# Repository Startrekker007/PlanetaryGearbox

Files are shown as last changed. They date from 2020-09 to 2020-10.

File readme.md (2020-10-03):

The submission for the assignment is in the folder FinalAssembly. Within there is another readme.md file which consists of the summary of the project.

The _Old folder consists of the working files during the project and they don't need to be seen, they're just in the git repository in case.

Viewing on Github is easier to read and view therefore the link is https://github.com/Startrekker007/PlanetaryGearbox

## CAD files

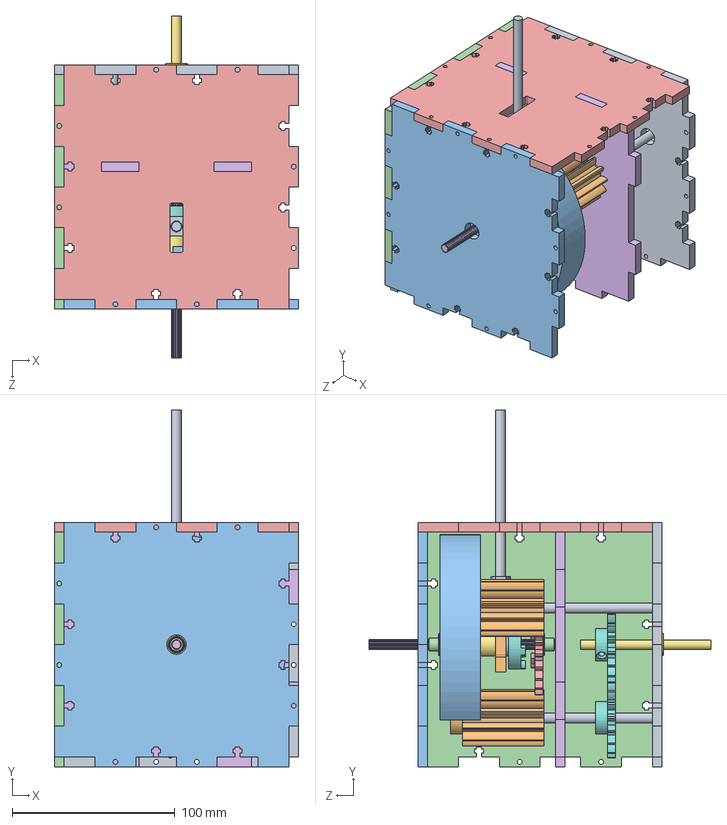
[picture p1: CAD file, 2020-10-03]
FinalAssembly/FinalAssemblyAnimation.SLDASM
150.0 x 218.9 x 210.0 mm
Shaft80mm
InputGear x 2
Shaft130mm x 4
PlanetGear x 3
RingGear
3x6ID_12OD_Flanged_Bearing x 2
SpacingWasher x 2
SunGear
SplinedShaft120mm
DogToothCollar
DogToothEnd
ShiftHolder
12mmID_Bearing

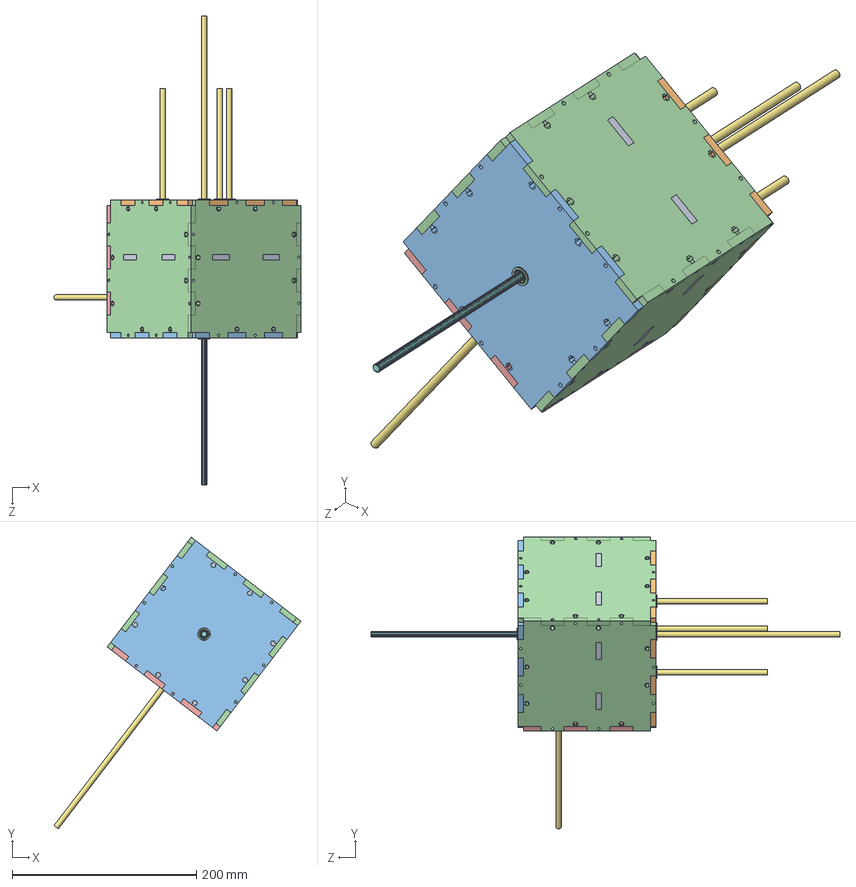
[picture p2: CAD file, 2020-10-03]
Saladworks/GearBoxWorking.SLDASM
268.0 x 316.5 x 509.0 mm
TripleInternal
InputSide
OutputSide
SlottedSide x 3
TopSide
InputGear x 2
Shaft250mm x 5
SplinedShaft250mm
planetgear x 3
sun
RingGear
535096.STEP
535096 bearing.STEP
CorrectDogTeeth
DoggedCollar
ShiftHolder

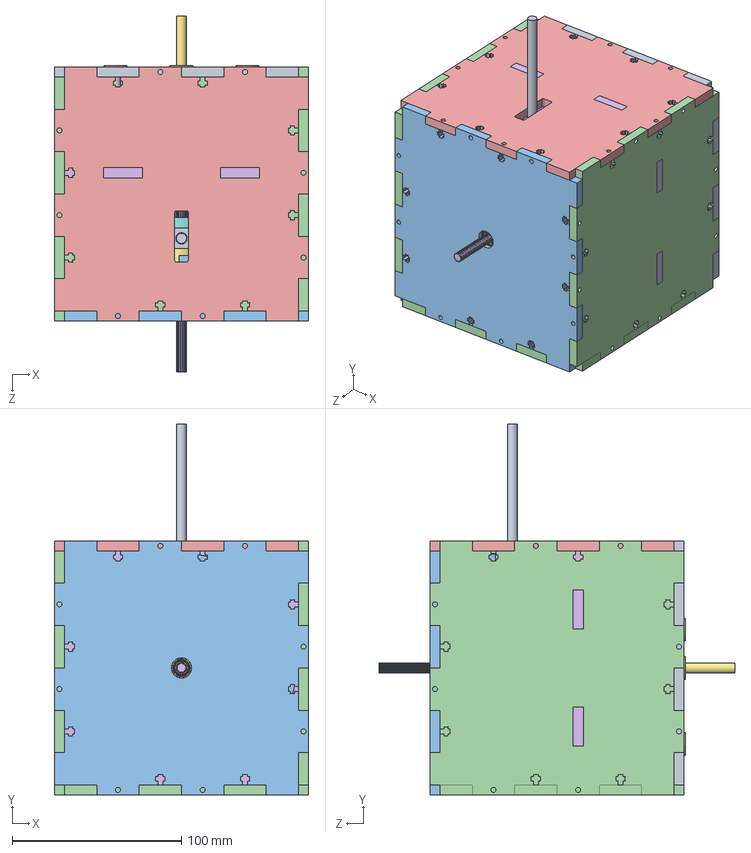
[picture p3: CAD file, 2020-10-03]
FinalAssembly/FinalAssembly.SLDASM
150.0 x 218.9 x 210.0 mm
InputSide
3x6ID_12OD_Flanged_Bearing x 11
OutputSide
SlottedSide x 3
TopSide
InternalWall
Shaft80mm
InputGear x 2
Shaft130mm x 4
PlanetGear x 3
RingGear
SpacingWasher x 2
SunGear
SplinedShaft120mm
DogToothCollar
DogToothEnd
ShiftHolder
12mmID_Bearing

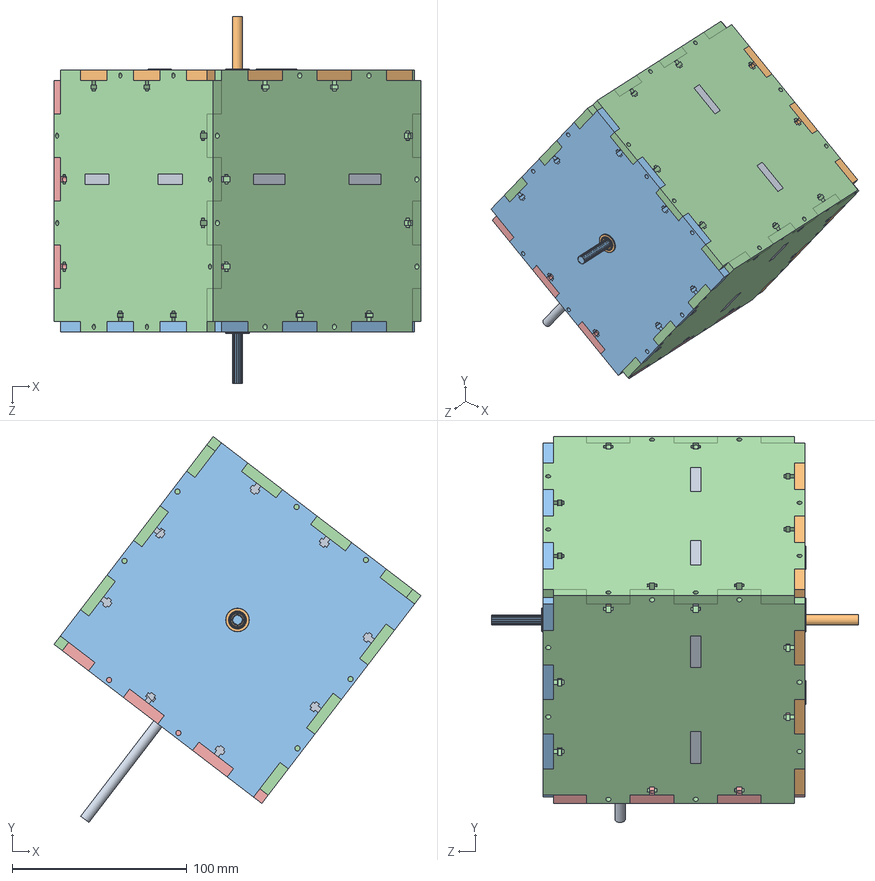
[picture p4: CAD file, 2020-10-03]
Saladworks/GearBoxRightLength.SLDASM
210.3 x 221.2 x 210.3 mm
TripleInternal
InputSide
OutputSide
SlottedSide x 3
TopSide
InputGear x 2
planetgear x 3
sun
RingGear
535096.STEP
535096 bearing.STEP
CorrectDogTeeth
DoggedCollar
ShiftHolder
Shaft130mm x 4
Shaft80mm
SplinedShaft120mm

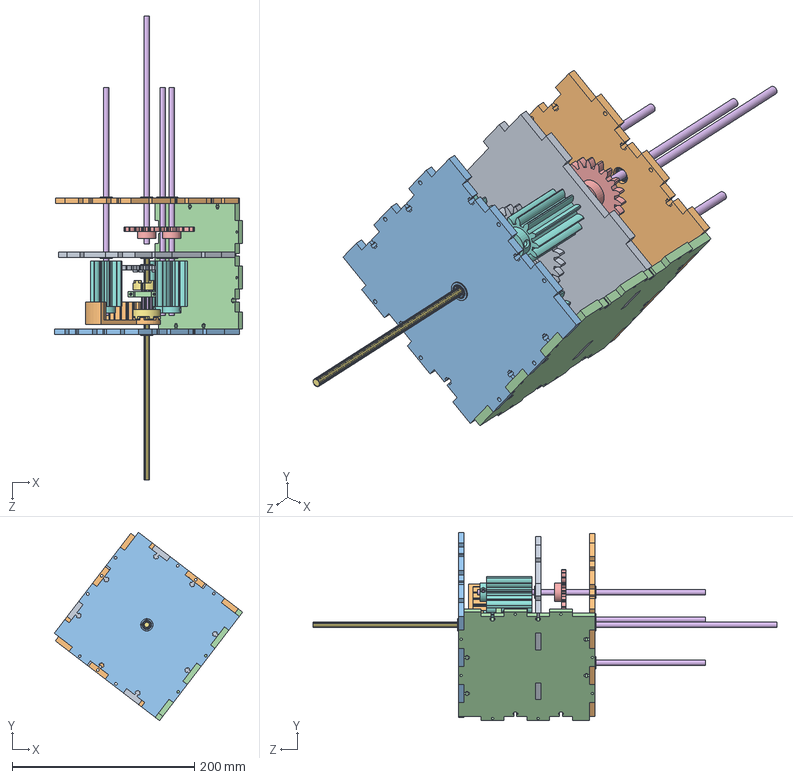
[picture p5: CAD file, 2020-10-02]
Saladworks/GearBox2019.SLDASM
206.6 x 206.6 x 509.0 mm
InputGear x 2
Shaft250mm x 4
SplinedShaft250mm
planetgear x 3
sun
RingGear
535096.STEP
535096 bearing.STEP
CorrectDogTeeth
DoggedCollar

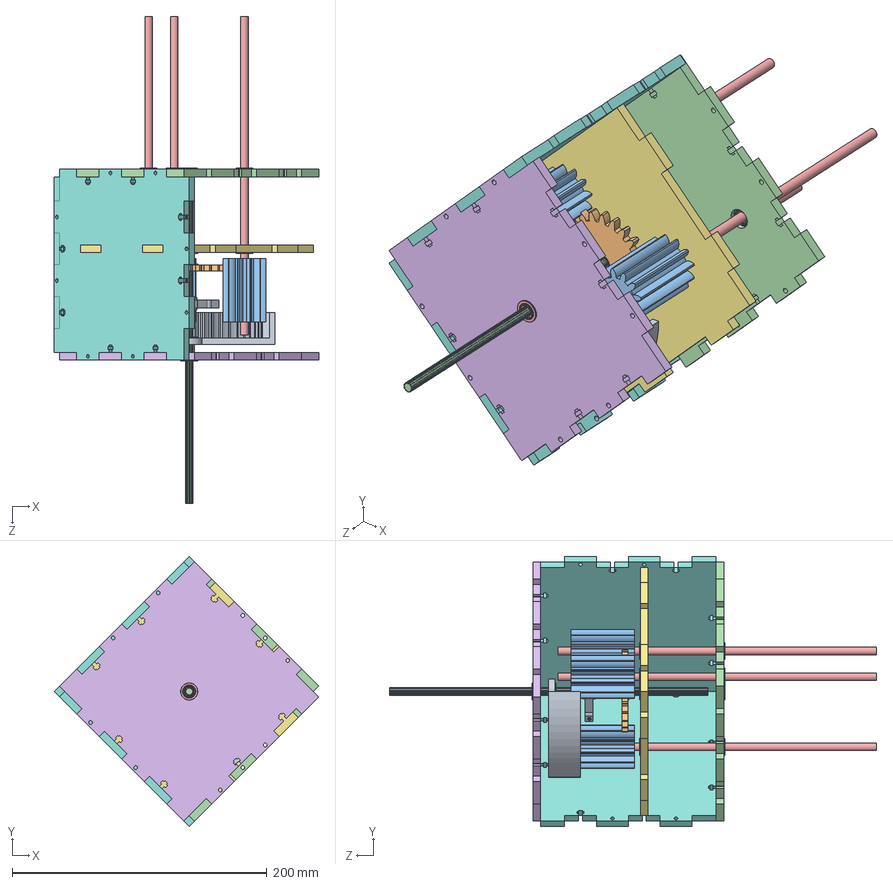
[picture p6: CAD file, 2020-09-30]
Saladworks/GearsWithBoxDemo.SLDASM
207.9 x 212.1 x 382.5 mm
RingGear
sun
planetgear x 3
SplinedShaft250mm
Shaft250mm x 3
5352201.STEP x 2
5352202.STEP x 2
5352203.STEP x 2
535096.STEP
535096 bearing.STEP
Collar
InputSide
535220.step x 9
OutputSide
TripleInternal
SlottedSide x 2

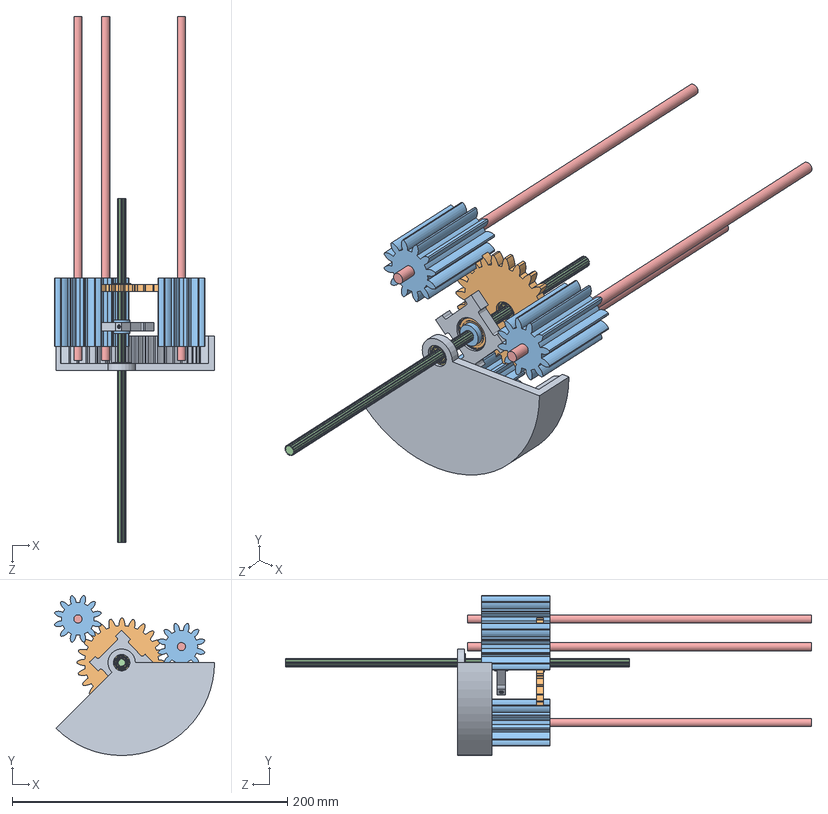
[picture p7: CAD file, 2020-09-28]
Saladworks/RealGears.SLDASM
116.3 x 116.3 x 382.5 mm
RingGear
sun
planetgear x 3
SplinedShaft250mm
Shaft250mm x 3
5352201.STEP x 2
5352202.STEP x 2
5352203.STEP x 2
535096.STEP
535096 bearing.STEP
Collar

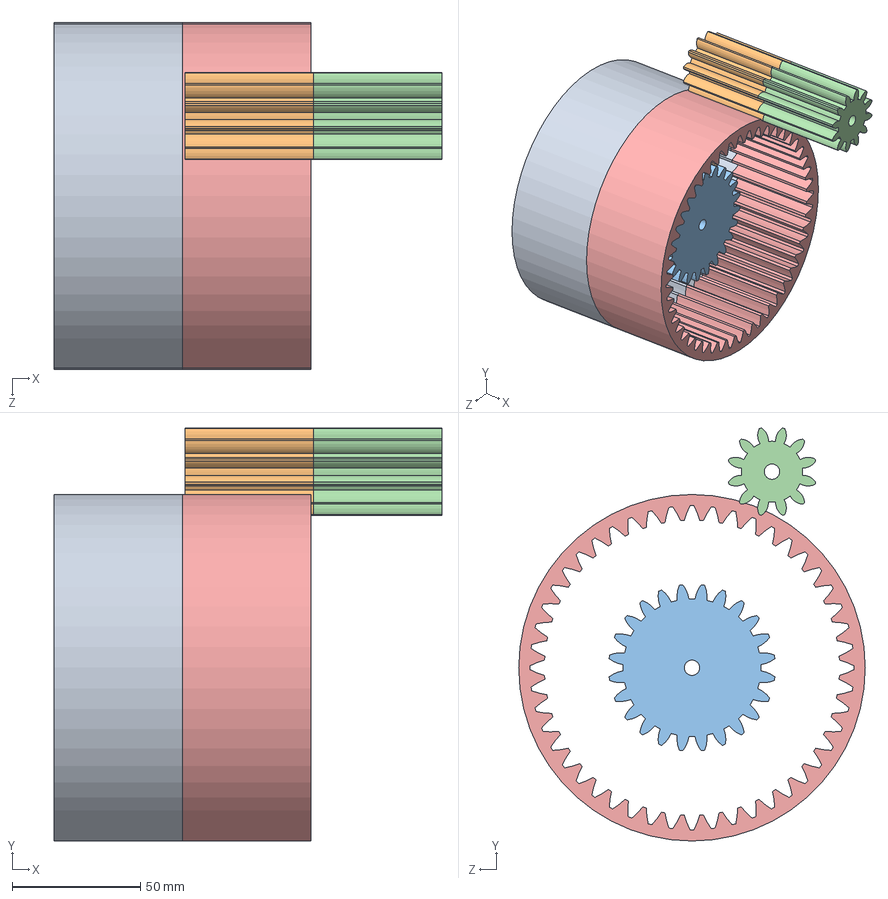
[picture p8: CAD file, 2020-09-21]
Saladworks/Planetary3.SLDASM
151.0 x 160.9 x 135.0 mm
internal spur gear_am
spur gear_am x 2
sun
PlanetGear
RingGear

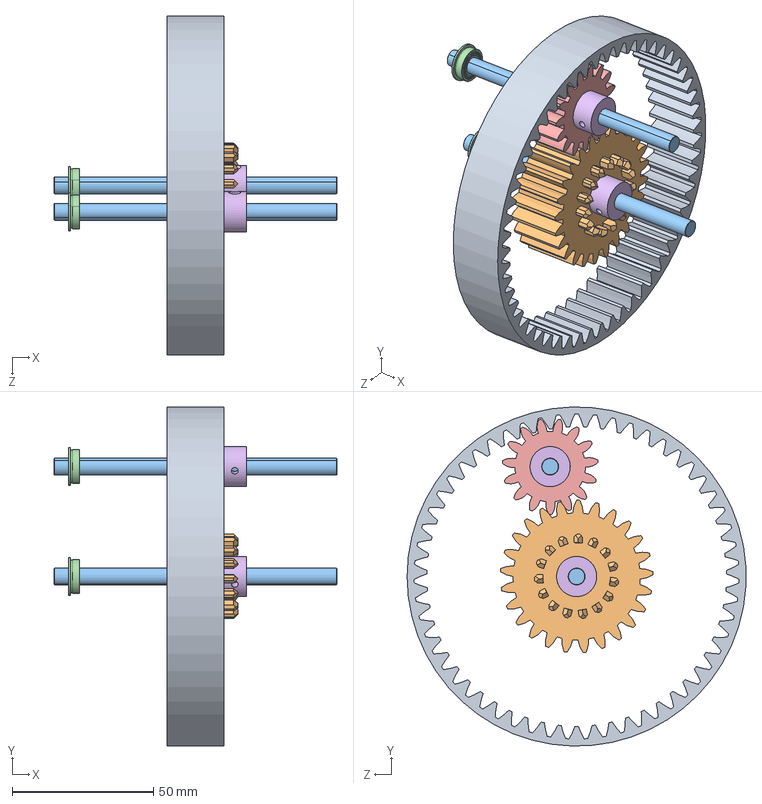
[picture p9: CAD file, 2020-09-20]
Saladworks/Gears.SLDASM
100.0 x 119.9 x 119.9 mm
internal spur gear_am
sungear
2100-0006-0100.step x 2
535220.step x 2
spur gear_am
ShaftStopper x 2

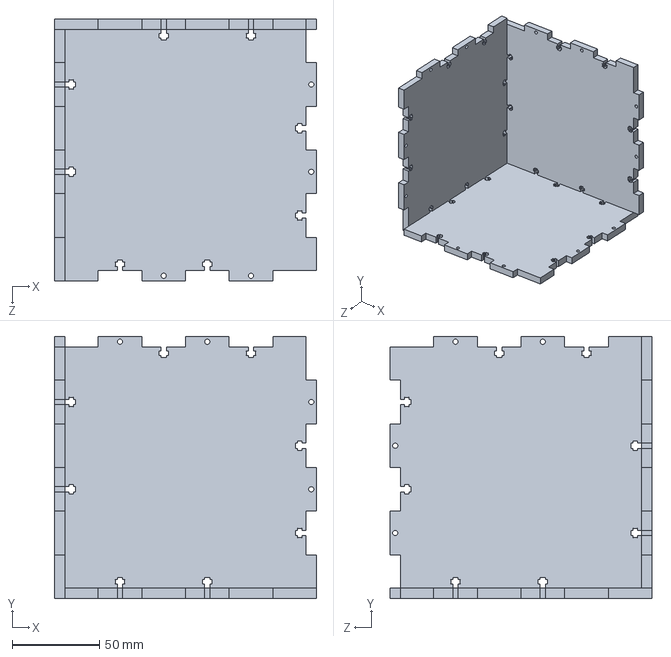
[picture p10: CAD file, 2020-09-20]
Saladworks/Assembledemo.SLDASM
150.0 x 150.0 x 150.0 mm
BlankSide x 3

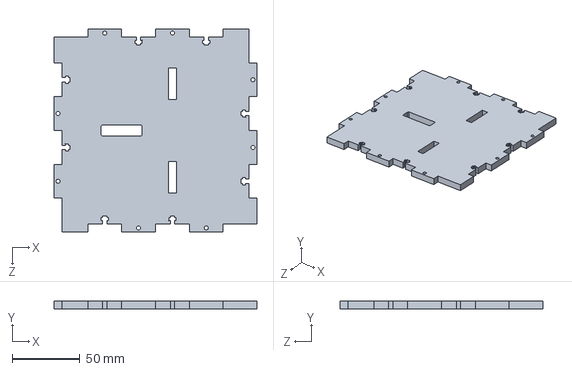
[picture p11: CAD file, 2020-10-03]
FinalAssembly/AcrylicCase/TopSide.SLDPRT
150.0 x 6.00 x 150.0 mm

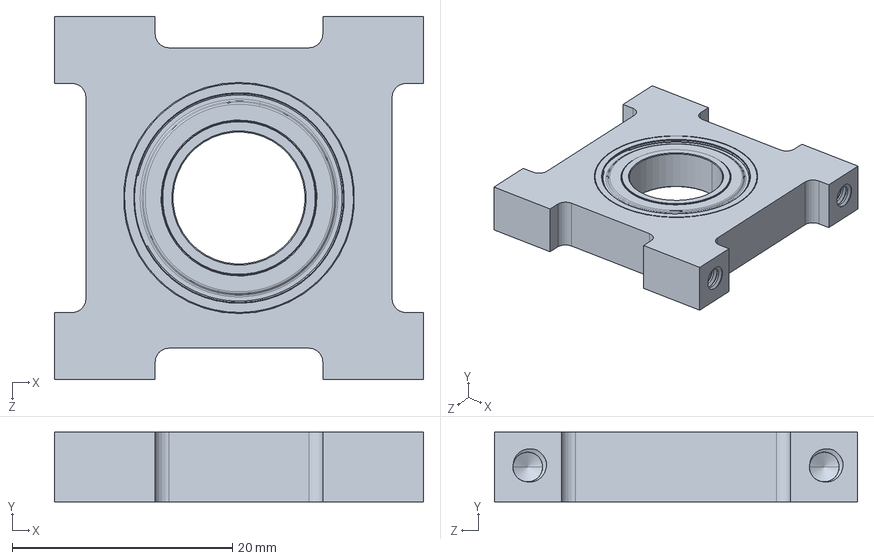
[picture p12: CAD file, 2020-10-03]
FinalAssembly/Bearings/12mmID_Bearing.SLDPRT
33.5 x 6.35 x 33.0 mm

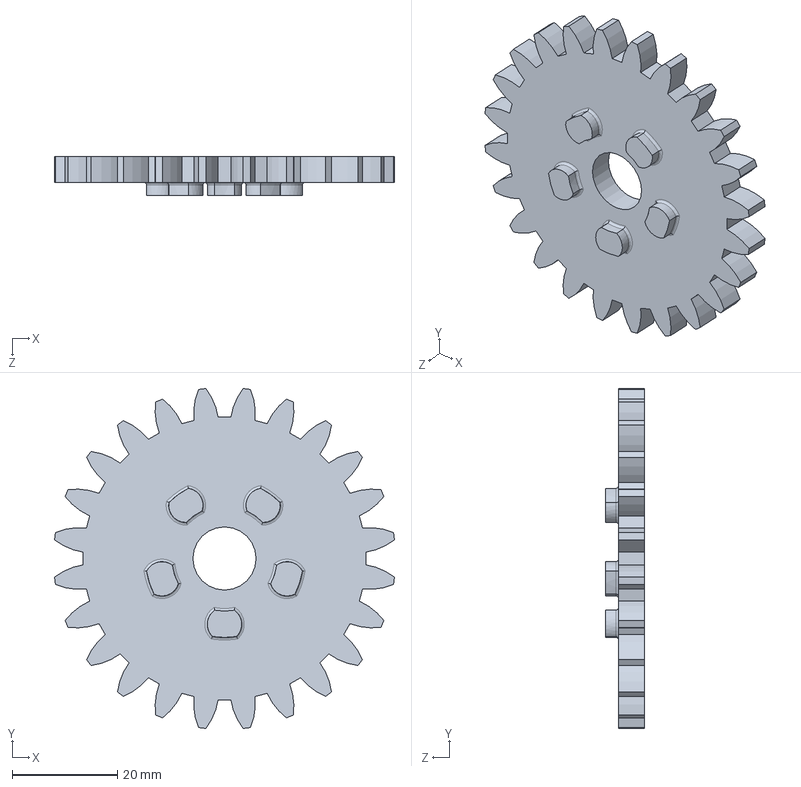
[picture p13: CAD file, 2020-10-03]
FinalAssembly/Gears/SunGear.SLDPRT
64.6 x 64.6 x 7.50 mm

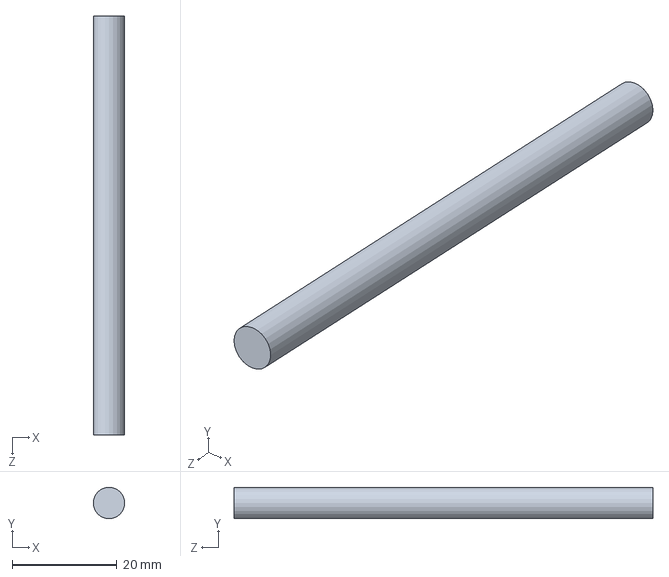
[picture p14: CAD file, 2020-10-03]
FinalAssembly/MetalShafts/Shaft80mm.SLDPRT
6.00 x 6.00 x 80.0 mm

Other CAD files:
Saladworks/realdeal.SLDASM
FinalAssembly/Transmission/DogToothCollar.SLDPRT
StepFiles/2100-0006-0100/2100-0006-0100.STEP
FinalAssembly/AcrylicCase/InternalWall.SLDPRT
FinalAssembly/AcrylicCase/6mm_Acrylic_1.SLDDRW
FinalAssembly/AcrylicCase/6mm_Acrylic_2.SLDDRW
FinalAssembly/AcrylicCase/InputSide.SLDPRT
FinalAssembly/AcrylicCase/InternalWall.SLDDRW
FinalAssembly/AcrylicCase/OutputSide.SLDPRT
FinalAssembly/AcrylicCase/SlottedSide.SLDPRT
FinalAssembly/Bearings/3x6ID_12OD_Flanged_Bearing.SLDPRT
FinalAssembly/Fabrication Outputs/3D Printing STLs/DogToothCollar.STL
FinalAssembly/Fabrication Outputs/3D Printing STLs/DogToothEnd.STL
FinalAssembly/Fabrication Outputs/3D Printing STLs/InputGear.STL
FinalAssembly/Fabrication Outputs/3D Printing STLs/PlanetGear.STL
FinalAssembly/Fabrication Outputs/3D Printing STLs/RingGear.STL
FinalAssembly/Fabrication Outputs/3D Printing STLs/ShiftHolder.STL
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

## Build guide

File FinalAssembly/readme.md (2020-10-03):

## Planetary Gearbox (Group 5)
##### Audrey Chan, Keshav Raj

#### Summary
This gearbox consists of a simple planetary gear drive system consisting of three planets, a ring gear and a sun gear. It also features central input and output shafts and the ability to shift between rotational directions on the output shaft.

The exterior box is made of laser cut 6mm acrylic while the gears themselves are to be 3D printed using ABS filament with at least 60% infill to provide the strength needed (as the input rotary motion specifications are unknown). For further details, please refer to the readme found within the fabrication outputs folder for 3D printing.

The gears all follow a standard which consists of a module of 2.5 and pressure angle of 20 degrees. As mentioned previously there are two drive gears to the output shaft which provide two different directions and rate of rotations. The two gears are the sun and ring gears.
The gear ratio between the output and input shafts when the sun gear is engaged is 2:1 (input : output). The gear ratio from when the ring gear is engaged is 4:1 in the opposite direction. As such this gearbox is a reduction gearbox.

In order to mount a bearing onto the shafts, the bearing must be heated in heated oil to expand it. Then it can be mounted onto a shaft and after it cools it will form a tight grip with the shaft and shouldn’t move around.

As the gear system is expected to be slow in rotational speed (it is plastic and ABS melts at 230 degrees and will erode quickly), epoxy can be used to mount the gears onto the bearings.

For additional assembly details regarding the gearbox, please refer to the file “instructions.pdf” which consists of a step by step set of instructions on assembling the gearbox and getting it ready for operation.

#### Video in Motion
Link: https://youtu.be/1ZXuh8vvWhE

Full disclosure for this we used the “animation” modelling and manually spun every gear instead of the “basic motion” technique. After playing with this for hours I think there’s just too much stuff for the system to calculate the physics in a coherent way. Parts would move that weren’t even “contact” tooled with anything and the teeth would just get stuck on themselves. You can see though in the video and by running the sim yourself that all the teeth mesh right and the movement makes sense.

Missing from this video is the action of the shifter which was too complex to make work in the vid. Basically the stick on the top pushes dog teeth gears into the sun or moon gear which connects the output splined shaft to that gear. Thus the output can be switched between gears.

#### BOM

| Item | Qty | Extra Details | Cost? | External Links: |
|---|---|---|---|---|
| ABS Filament | 178g (66.86m) | 1.75mm filament | $34.99 USD/1KG | https://www.amazon.com/Dremel-Nylon-Printer-Filament-Diameter/dp/B076MBTJBR/ |
| Acrylic (clear) | 2x 600x400 Sheets | 6mm thickness | $25.81 NZD Exc GST | https://cambrianplastics.co.nz/product/acrylic-clear-cut-to-size-2/ |
| 6 mm ID x 12mm OD Flanged Ball Bearing | 11 | Servocity Part: 535220 | $18.65 USD | https://www.servocity.com/6mm-id-x-12mm-od-flanged-ball-bearing-2-pack/ |
| 12mm Bore Side Tapped Pillow Block | 1 | Servocity Part: 535096 | $8.49 USD | https://www.servocity.com/12mm-bore-side-tapped-pillow-block/ |
| 720 mm of silver steel rod | 1 | | ~$13 NZD | https://tradetools.co.nz/products/silver-steel-6mmx36-length |
| M3x12 screws | 48 | From Tim | You have plenty | |
| M3x16 screws | 5 | From Tim | You have plenty | |
| UNC 6-32 30mm screws | 2 | | $1.25 USD | https://www.amazon.com/Phobya-UNC-6-32-30mm-Screws/dp/B004CLJLKI |
| M3 Nuts | 48 | From Tim | You have plenty | |
| Decorative Sticker Sheet | 1 | I demand you put stickers on it (don’t have to be these stickers, just anything with a rocket) | $8.95 USD | https://www.amazon.com/SPACE-Self-adhesive-Reflective-Decorative-Scrapbook/dp/B076CWYRM2/ref=sr_1_3 |

#### Contributions

###### Keshav:

* Created the gears in Solidworks
* Created the gear system assembly.
* Generated fabrication outputs
* Explanation of how to optimally 3D print the ABS components.

###### Audrey:

* Created Box
* Created Motion Study
* Created Assembly Instructions
* Filmography and Sound Design

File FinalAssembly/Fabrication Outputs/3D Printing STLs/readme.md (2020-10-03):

### Printing Requirements
All components within have to be 3D printed using ABS plastic filament at 60% infill. Below shows images of optimal build plate placements followed by material requirements.

##### Ring Gear
The ring gear must be printed as shown by the following figure: <br>

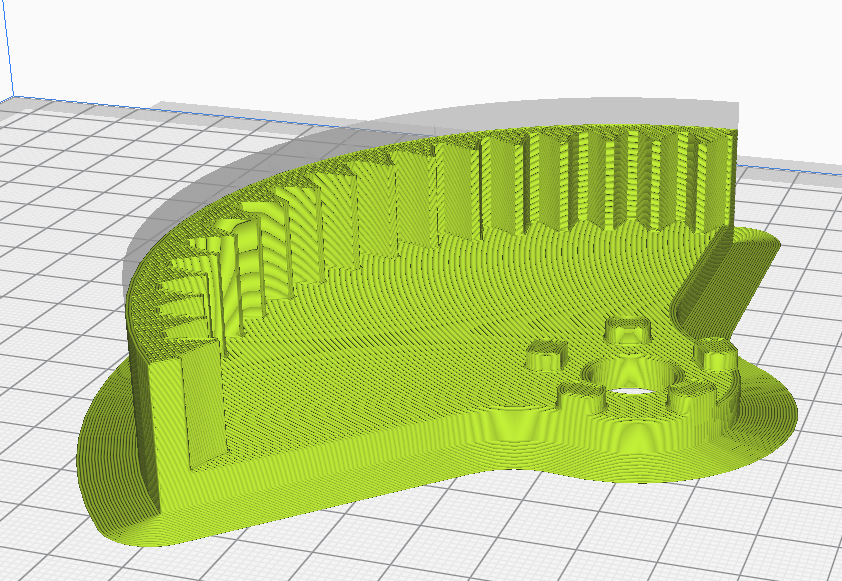
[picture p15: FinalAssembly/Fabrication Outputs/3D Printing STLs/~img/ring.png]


The total ABS requirement for this part is 43g (16.19m).

##### Input drive gears
The drive gears must be printed as shown by the following figure: <br>

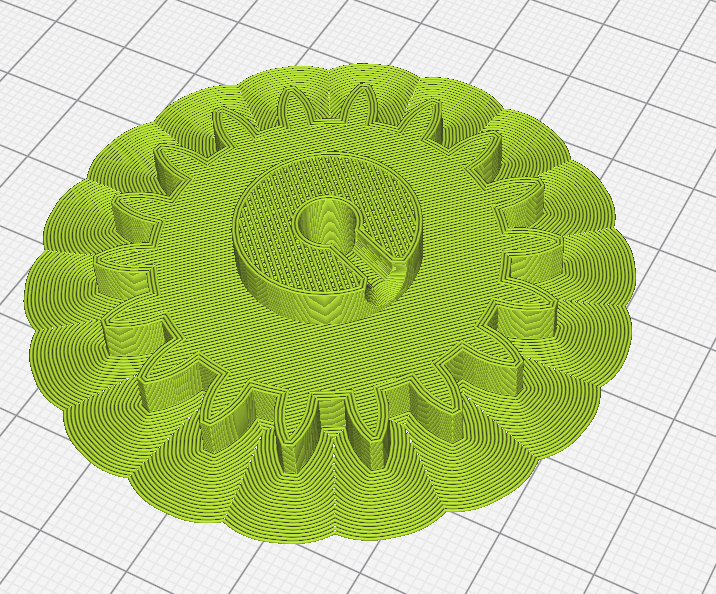
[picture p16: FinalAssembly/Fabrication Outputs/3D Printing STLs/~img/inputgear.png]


The total ABS requirement for this part is 9g (3.31m) each. Total: 18g (6.62m).

Special consideration for this gear is that the keyway screw hole may not print correctly if a print cooler fan isn't equipped on the printer.

The overhang may not print correctly as a result. Therefore if necessary, the fabricator can add supports touching the model to ensure the screw hole prints correctly.

##### Planet gears
The planet gears of which THREE are required must be printed as per the following figure <rb>

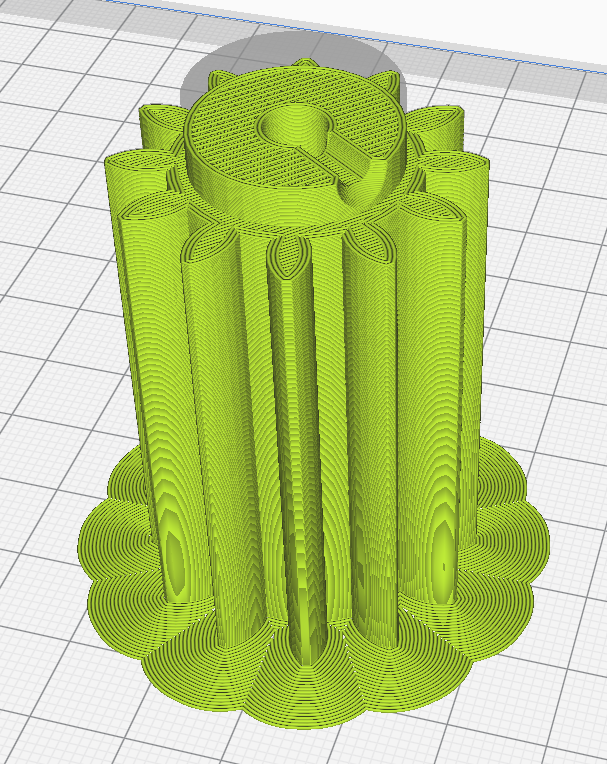
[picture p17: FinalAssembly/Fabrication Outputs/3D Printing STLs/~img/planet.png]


The total ABS requirement each is 27g (10.27m) with a total of 81g (30.81m).

Special consideration for this gear is that the keyway screw hole may not print correctly if a print cooler fan isn't equipped on the printer.

The overhang may not print correctly as a result. Therefore if necessary, the fabricator can add supports touching the model to ensure the screw hole prints correctly.

##### Sun gear
The sun gear must be printed as per the following:

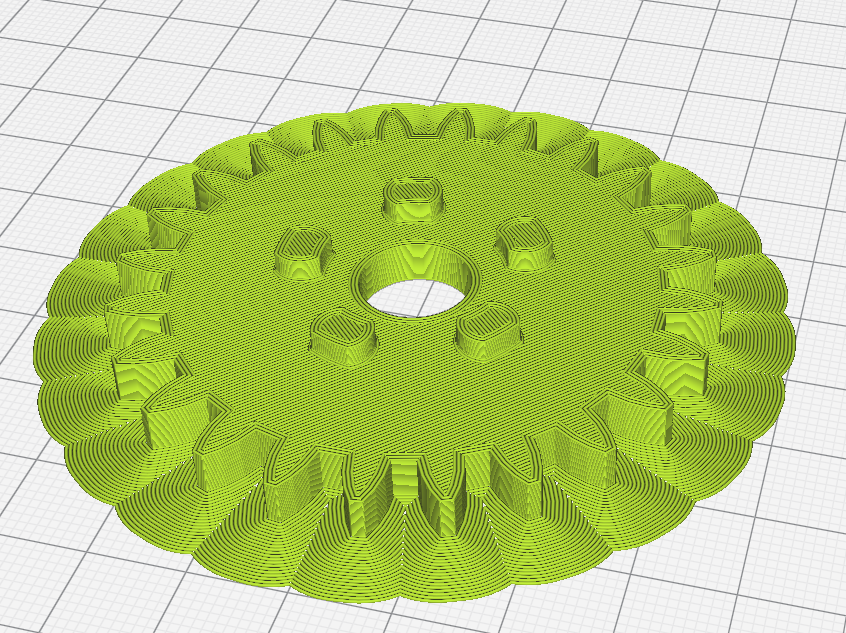
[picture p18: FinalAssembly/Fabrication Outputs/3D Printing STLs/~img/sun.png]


The total ABS requirement for this is 12g (4.71m).

##### Dog Gear with Collar
This part must be printed as per the following figure:

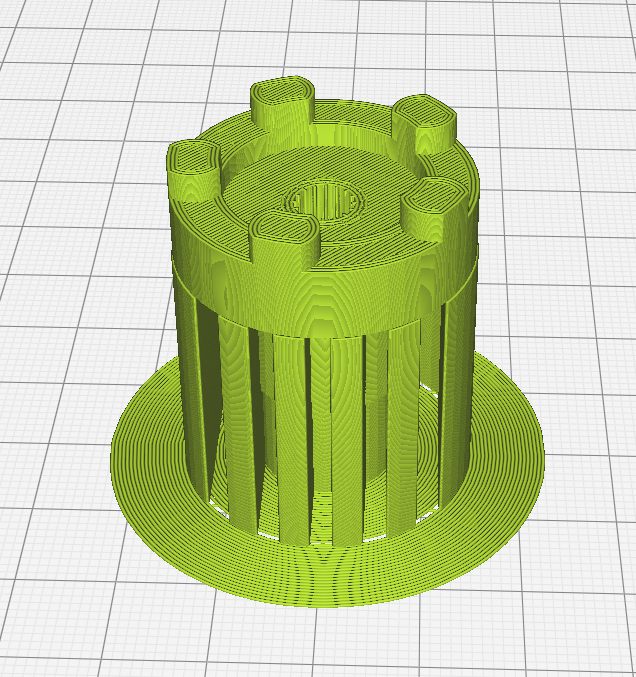
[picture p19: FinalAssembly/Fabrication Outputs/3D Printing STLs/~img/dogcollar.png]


The total ABS requirement for this is 11g (3.99m).

This part must be printed upside down (while normally one would expect to print it the other way to reduce support usage) but it is necessary that the spline teeth must be correctly printed and this is best accomplished if they are printed directly from the build plate.

It is ideal that one use a printer with a smaller nozzle diameter to increase the spline teeth's resolution. But a printer with a regular 0.4mm nozzle should also suffice.

##### Dog Gear
This part must be printed as per the following figure:

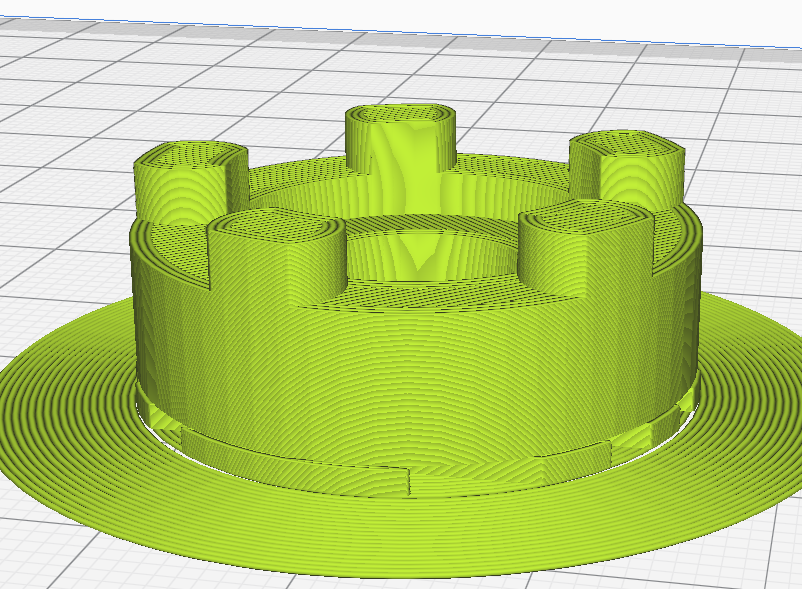
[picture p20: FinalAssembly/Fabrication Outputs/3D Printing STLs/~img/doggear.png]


The total ABS requirement for this is 5g (1.71m).

##### Shift Holder
This part must be printed as per the following figure:

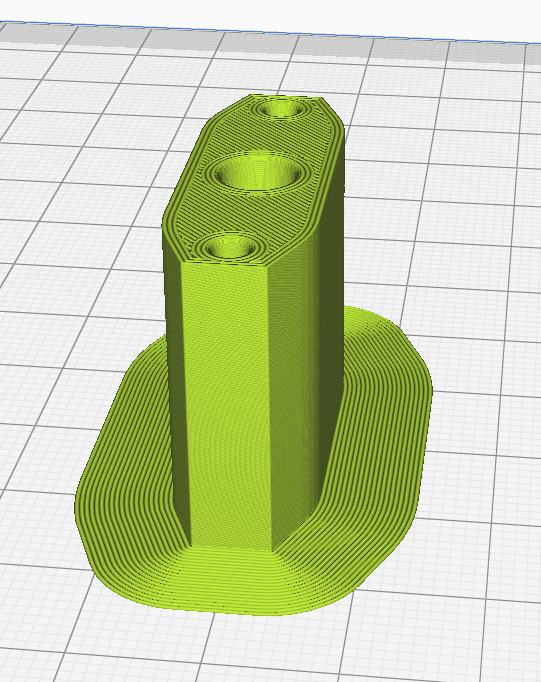
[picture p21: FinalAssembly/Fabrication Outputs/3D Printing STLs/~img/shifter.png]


The total ABS requirement for this is 7g (2.62m).

##### Spacing Washers
This part must be printed as per the following figure:

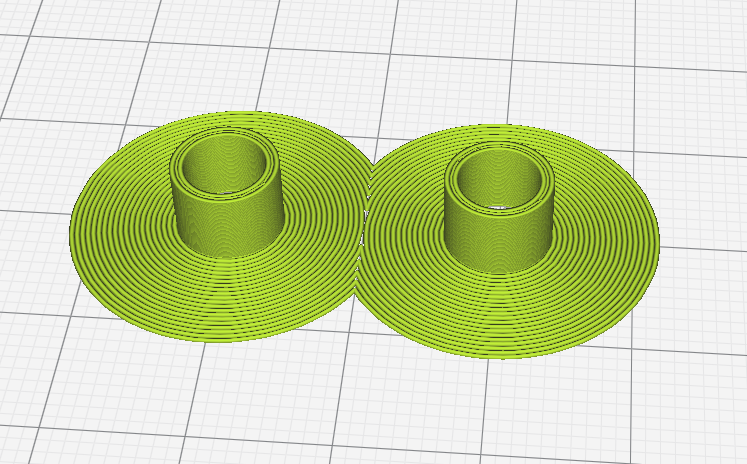
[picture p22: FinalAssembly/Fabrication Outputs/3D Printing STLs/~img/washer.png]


Together these parts require 1g of ABS (0.21m).

These two parts can be printed at once, however must be spaced out by at least 20mm to prevent stringing between the two (in case of poor retraction or bowden feed setups).

##### Total Material Requirement:
In order to print all the required parts to produce the gearbox, the fabricator will require 178g of ABS. Or 66.86m of 1.75mm ABS filament.

From Amazon, Dremel 1.75mm ABS filament (Black) 1KG costs $34.99 USD, the total used for this job would cost $6.23.

Link: https://www.amazon.com/Dremel-Nylon-Printer-Filament-Diameter/dp/B076MBTJBR/

The sliced renders and filament estimations were done using Ultimaker Cura (With the Tevo Tarantula (Reprap) as the printer).

Some of the models above are shown with a "sectional" view to show the interior infill. Brim type build adhesion is COMPULSORY for the larger prints e.g. Ring gear otherwise warping may occur.

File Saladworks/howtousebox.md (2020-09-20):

Assembledemo uses BlankSide to make a demo enclosure, use that if you want to compare your internal components for size or whatnot

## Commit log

2020-09-19 Adding some steps and a gear assembly
    [2100-0006-0100.STEP, 535220.STEP, Gears.SLDASM]
2020-09-19 Adding more gears and fastening to shaft
    [Gears.SLDASM, ShaftStopper.SLDPRT]
2020-09-20 Adding shit
    [Gears.SLDASM, Planetary3.SLDASM, dawg_gear.SLDPRT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]
2020-09-21 Fixing the assembly
    [Planetary3.SLDASM]
2020-09-21 Revert "toolboxbrah"
    This reverts commit 1f9f4b05fc86e3d1be0d4ff20d3b6ea926aff8c2.
    [Assembledemo.SLDASM, BlankInternal.SLDPRT, BlankSide.SLDPRT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]
2020-09-21 adding proper
    [Planetary3.SLDASM, sun.SLDPRT, sunboi.SLDPRT]
2020-09-21 Adding gears
    [535096 assembly.STEP, Collar.SLDPRT, Planetary3.SLDASM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]
2020-09-28 Adding dog teeth
    [CorrectDogTeeth.SLDPRT, DogGear.SLDPRT, RealGears.SLDASM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]
2020-09-30 Add files via upload
    GearsWithBoxDemo (Put the gears in box to demo size)
    InputSide (Input side of box)
    OutputSide (Output Side of Box)
    SlottedSide (Normal Sides, just not top)
    TripleInternal (Supporting wall inside)
    [GearsWithBoxDemo.SLDASM, InputSide.SLDPRT, OutputSide.SLDPRT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]
2020-10-02 Creating full assembly from scratch because saladworks 2019 sucks cock
    [2100-0006-0100.SLDPRT, 535096 assembly.STEP.SLDASM, 535220.SLDPRT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]
2020-10-02 adding keyways, god gears
    [535220.SLDPRT, Collar.SLDPRT, CorrectDogTeeth.SLDPRT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]
2020-10-02 Joining collar with one dog gear
    [DoggedCollar.SLDPRT, GearBox2019.SLDASM]
2020-10-03 Direction readme and cleaning directory
    [2100-0006-0100.SLDPRT, 2100-0006-0100.STEP, 535096 assembly.STEP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]
2020-10-03 Adding forgotten spacing washer fab output
    [SpacingWasher.STL]
